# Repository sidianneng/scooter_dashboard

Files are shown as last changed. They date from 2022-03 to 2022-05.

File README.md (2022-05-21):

# 滑板车定制仪表盘

## 1 项目概述

该仪表盘基于ninebot的E22滑板车进行设计。

**在兼容原始仪表盘的所有功能的前提下，同时将官方手机端的功能也集成到了其中。**

这样极大的提高了使用的便捷性。

## 2 功能介绍
该仪表盘共计有4个界面，分别对应不同的功能：
### 2.1 主界面
主界面中100%还原了官方仪表盘的原始状态。支持显示的内容如下：
* 实时速度
* 电量情况
* 充电情况
* 速度单位
* 蓝牙状态
* 运动模式
* 错误提示

图片如下：

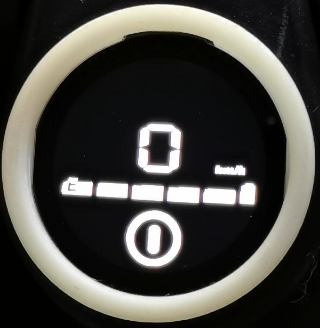
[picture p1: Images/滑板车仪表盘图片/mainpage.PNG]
mainpage


### 2.2 上锁解锁界面
该界面可以通过长按触摸屏实现对滑板车的上锁解锁，避免了以往手机app连接的繁琐操作。

图片如下：

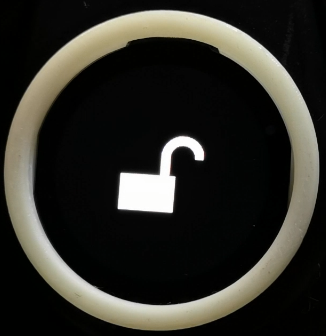
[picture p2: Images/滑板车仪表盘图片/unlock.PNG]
unlock

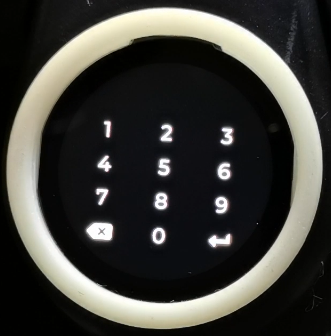
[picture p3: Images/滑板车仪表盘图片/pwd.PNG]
pwd


### 2.3 续航数据显示界面
该界面显示了如下信息：
* 剩余续航
* 剩余电量
* 总里程数

图片如下：

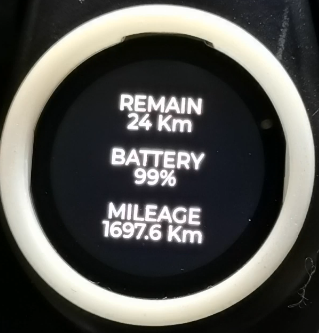
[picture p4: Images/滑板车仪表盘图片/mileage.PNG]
mileage


### 2.4 设置界面
该界面实现了滑板车的一些配置功能，具体如下：

* 开启关闭定速巡航
* 设置能量回收强度
* 设置上锁解锁密码

相关图片如下：

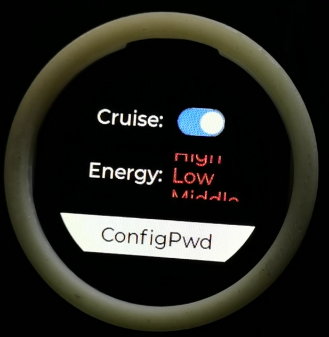
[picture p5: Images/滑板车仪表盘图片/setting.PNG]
setting

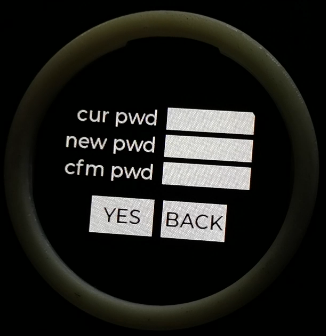
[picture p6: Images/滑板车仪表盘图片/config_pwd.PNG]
config_pwd


## 3 关键性功能原理介绍
该仪表盘中有两个核心功能点：

* 原始仪表盘数据解析
* 原始通讯协议数据解析

### 3.1 原始仪表盘数据解析
原始仪表盘的数据是通过蓝牙芯片控制一个数码管驱动芯片(TM1650)实现的，其中使用I2C作为通讯接口。我们通过解析其I2C通讯的数据内容，结合数码管芯片的数据手册。这样就能获取到完整的仪表盘数据了。

示意图如下：

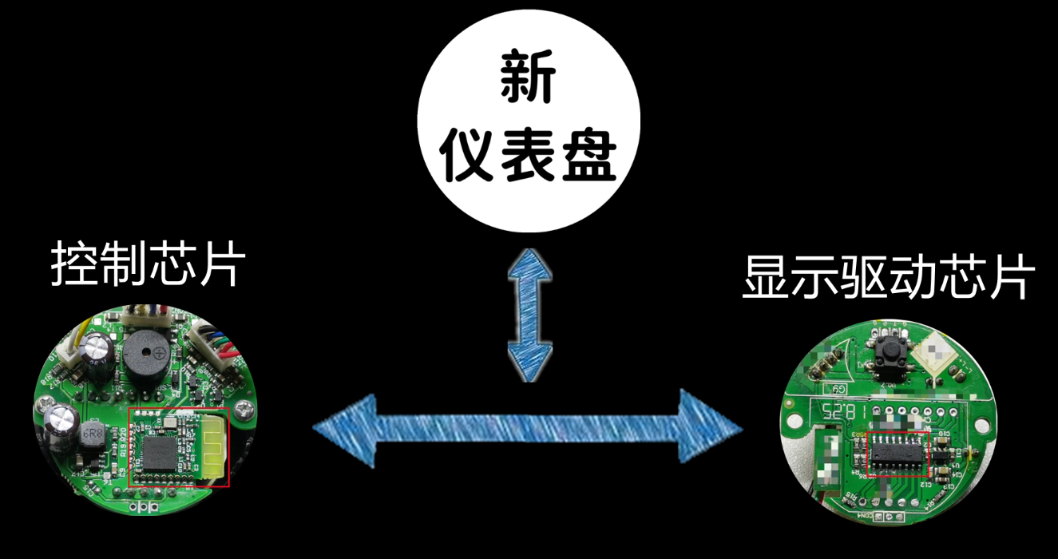
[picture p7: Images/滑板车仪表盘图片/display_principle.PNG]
display_principle


### 3.2 原始通讯协议数据解析
原始仪表盘和主板之间通过单线串口实现数据通讯，我们通过将新仪表盘连接到它们之间，通过截取和转发它们间的通讯内容，在必要时加入我们需要的数据，这样就能实现对滑板车的更多功能控制。

示意图如下：

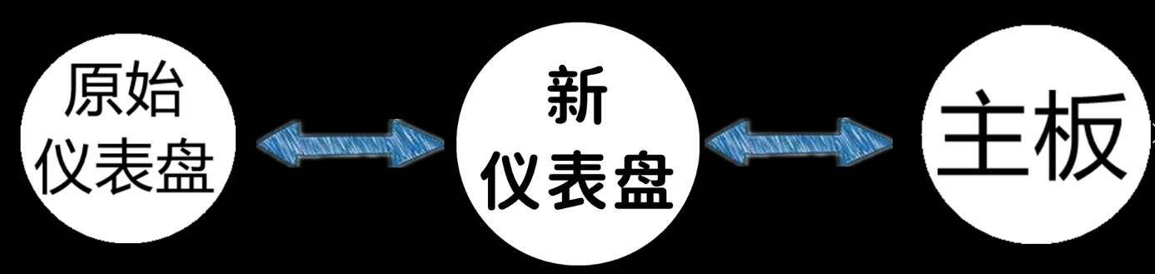
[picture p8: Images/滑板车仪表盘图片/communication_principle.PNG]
communication_principle


## 4 鸣谢
该项目的软件框架是基于[X-TRACK](https://github.com/FASTSHIFT/X-TRACK)进行二次开发的。

X-TRACK是一个很不错的开源项目，其代码逻辑实现非常清晰和优美，另外其处理issue的速度也非常快。在我开发的过程中提供了很多帮助。在这里对其表示衷心的感谢。希望该项目能越来越好。

***如果使用过程中有任何问题，欢迎在issue中进行提问~***

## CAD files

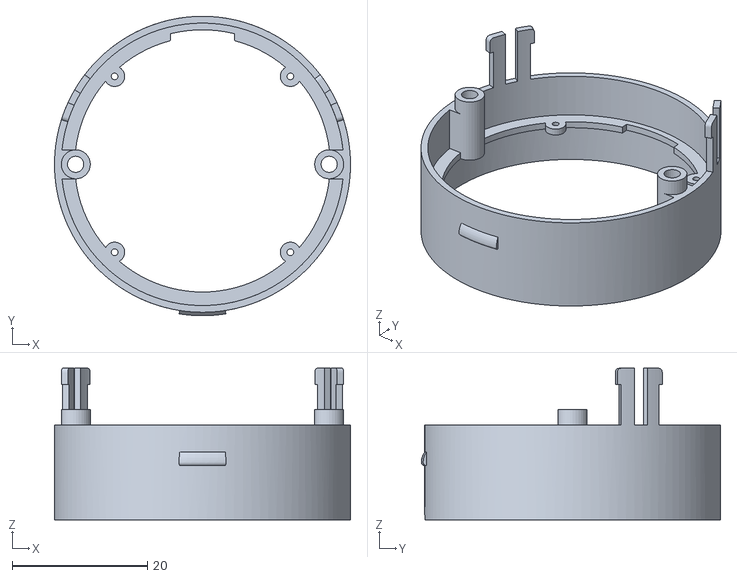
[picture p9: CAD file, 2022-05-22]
3D Model/scooter_panel_main v68.stl
43.7 x 44.2 x 22.4

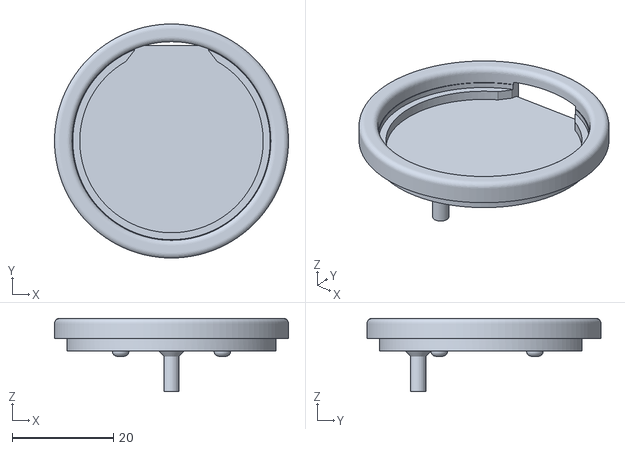
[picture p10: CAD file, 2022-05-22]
3D Model/scooter_panel_lcd v31.stl
46.2 x 46.2 x 14.5

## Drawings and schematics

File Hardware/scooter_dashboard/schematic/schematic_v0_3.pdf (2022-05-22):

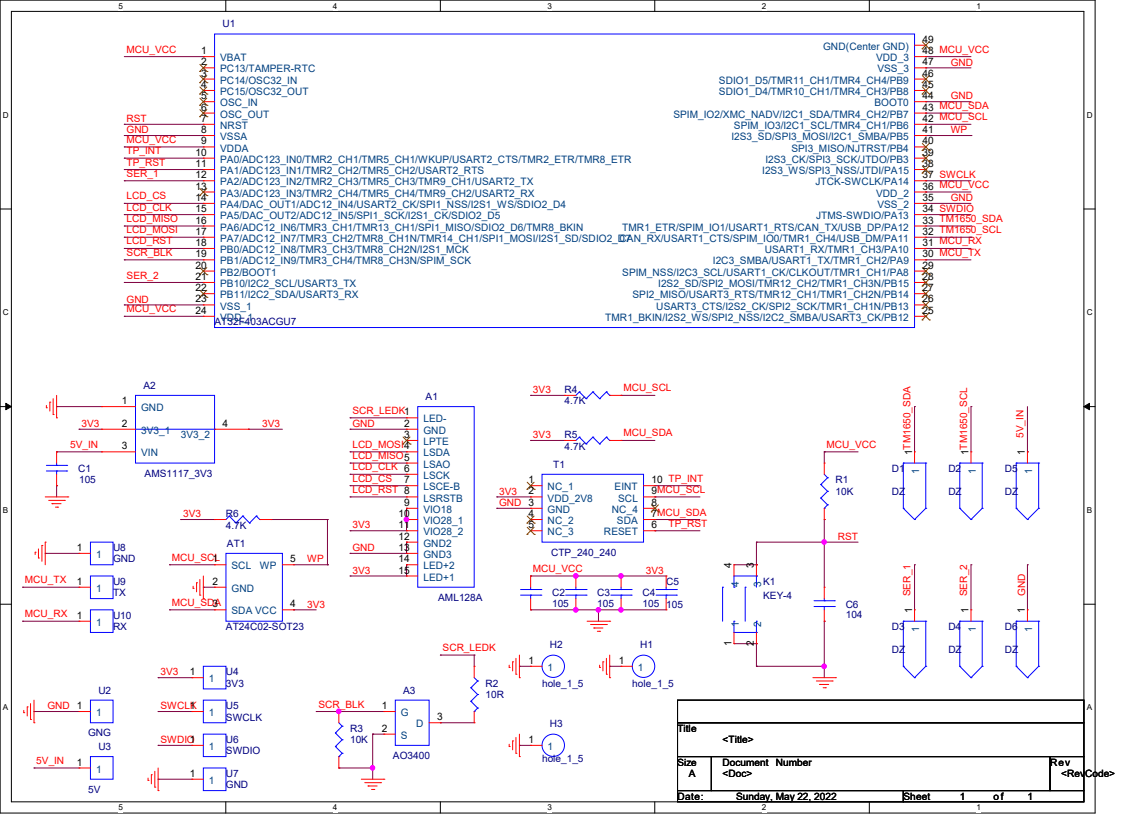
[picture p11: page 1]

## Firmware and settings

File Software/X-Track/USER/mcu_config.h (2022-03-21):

/*
 * MIT License
 * Copyright (c) 2019-2021 _VIFEXTech
 *
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
 * THE SOFTWARE IS PROVIDED "AS IS", WITHOUT WARRANTY OF ANY KIND, EXPRESS OR
 * IMPLIED, INCLUDING BUT NOT LIMITED TO THE WARRANTIES OF MERCHANTABILITY,
 * FITNESS FOR A PARTICULAR PURPOSE AND NONINFRINGEMENT. IN NO EVENT SHALL THE
 * AUTHORS OR COPYRIGHT HOLDERS BE LIABLE FOR ANY CLAIM, DAMAGES OR OTHER
 * LIABILITY, WHETHER IN AN ACTION OF CONTRACT, TORT OR OTHERWISE, ARISING FROM,
 * OUT OF OR IN CONNECTION WITH THE SOFTWARE OR THE USE OR OTHER DEALINGS IN THE
 * SOFTWARE.
 */
#if 1

#ifndef __MCU_CONFIG_H
#define __MCU_CONFIG_H

/*=========================
   MCU configuration
 *=========================*/

/* System tick */
#define SYSTICK_TICK_FREQ                   1000 // Hz
#define SYSTICK_PRIORITY                    0

/* Hardware Serial */
#define SERIAL_RX_BUFFER_SIZE               512
#define SERIAL_PREEMPTIONPRIORITY_DEFAULT   1
#define SERIAL_SUBPRIORITY_DEFAULT          3
#define SERIAL_CONFIG_DEFAULT               SERIAL_8N1

#define SERIAL_1_ENABLE                     1
#if SERIAL_1_ENABLE
#  define SERIAL_1_USART                    USART1
#  define SERIAL_1_IRQ_HANDLER_DEF()        void USART1_IRQHandler(void)
#endif

#define SERIAL_2_ENABLE                     0
#if SERIAL_2_ENABLE
#  define SERIAL_2_USART                    USART2
#  define SERIAL_2_IRQ_HANDLER_DEF()        void USART2_IRQHandler(void)
#endif

#define SERIAL_3_ENABLE                     0
#if SERIAL_3_ENABLE
#  define SERIAL_3_USART                    USART3
#  define SERIAL_3_IRQ_HANDLER_DEF()        void USART3_IRQHandler(void)
#endif

/* Wire (Software I2C) */
#define WIRE_USE_FULL_SPEED_I2C             0
#define WIRE_SDA_PIN                        PB7
#define WIRE_SCL_PIN                        PB6
#define WIRE_DELAY                          5
#define WIRE_BEGIN_TIMEOUT                  100 // ms
#define WIRE_BUFF_SIZE                      32

/* SPI Class */
#define SPI_CLASS_AVR_COMPATIBILITY_MODE    1
#define SPI_CLASS_PIN_DEFINE_ENABLE         0

#define SPI_CLASS_1_ENABLE                  1
#if SPI_CLASS_1_ENABLE
#  define SPI_CLASS_1_SPI                   SPI1
#endif

#define SPI_CLASS_2_ENABLE                  1
#if SPI_CLASS_2_ENABLE
#  define SPI_CLASS_2_SPI                   SPI2
#endif

#define SPI_CLASS_3_ENABLE                  0
#if SPI_CLASS_3_ENABLE
#  define SPI_CLASS_3_SPI                   SPI3
#endif

/* WString */
#define WSTRING_MEM_CUSTOM                  1
#if WSTRING_MEM_CUSTOM
#  define WSTRING_MEM_INCLUDE               "lvgl/lvgl.h"
#  define WSTRING_MEM_REALLOC               lv_mem_realloc
#  define WSTRING_MEM_FREE                  lv_mem_free
#endif

/* Print */
#define PRINT_PRINTF_BUFFER_LENGTH          128

/* GPIO */
#define GPIO_MAX_SPEED_DEFAULT              GPIO_MaxSpeed_50MHz

/* External Interrupt  */
#define EXTI_PREEMPTIONPRIORITY_DEFAULT     2
#define EXTI_SUBPRIORITY_DEFAULT            1

/* Timer Interrupt */
#define TIMER_PREEMPTIONPRIORITY_DEFAULT    0
#define TIMER_SUBPRIORITY_DEFAULT           3

/* Tone */
#define TONE_TIMER_DEFAULT                  TIM1
#define TONE_PREEMPTIONPRIORITY_DEFAULT     0
#define TONE_SUBPRIORITY_DEFAULT            1

/* PWM */
#define PWM_DUTYCYCLE_DEFAULT               1000
#define PWM_FREQUENCY_DEFAULT               10000

/* Digital Tube(TM1650) decode */
#define DIGITAL_TUBE_SCL_PIN								PA11
#define DIGITAL_TUBE_SDA_PIN								PA12

#endif

#endif

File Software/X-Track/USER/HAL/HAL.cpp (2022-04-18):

#include "HAL.h"
#include "App/Version.h"
#include "MillisTaskManager/MillisTaskManager.h"

static MillisTaskManager taskManager;

#if CONFIG_SENSOR_ENABLE
static bool IsWireInitSuccess = false;

static void HAL_Sensor_Init()
{
    IsWireInitSuccess = (HAL::I2C_Scan() > 0);

    if(!IsWireInitSuccess)
    {
        Serial.println("I2C: disable sensors");
        return;
    }

#if CONFIG_SENSOR_IMU_ENABLE
    HAL::IMU_Init();
#endif

#if CONFIG_SENSOR_MAG_ENABLE
    HAL::MAG_Init();
#endif
}

static void HAL_SensorUpdate()
{
    if(!IsWireInitSuccess)
    {
        return;
    }

#if CONFIG_SENSOR_IMU_ENABLE
    HAL::IMU_Update();
#endif

#if CONFIG_SENSOR_MAG_ENABLE
    HAL::MAG_Update();
#endif
}
#endif

static void HAL_TimerInterrputUpdate()
{
    HAL::Power_Update();
    HAL::Encoder_Update();
    HAL::Audio_Update();
}

void HAL::HAL_Init()
{
    Serial.begin(115200);
    Serial.println(VERSION_FIRMWARE_NAME);
    Serial.println("Version: " VERSION_SOFTWARE);
    Serial.println("Author: "  VERSION_AUTHOR_NAME);
    Serial.println("Project: " VERSION_PROJECT_LINK);

    FaultHandle_Init();

    Memory_DumpInfo();
	
		/*
			We need to init the hardware of scooter.
			Because we need to make sure the hardware ready
			to work before the origin hardware of scooter 
			start working.
		*/
		HalfDuplexSerial_Init();
		Scooter_Specify_Hardware_Init();

	  EEPROM_Init();
    //Power_Init();
    Backlight_Init();
    //Encoder_Init();
    //Clock_Init();
    //Buzz_init();
    //GPS_Init();
#if CONFIG_SENSOR_ENABLE
    HAL_Sensor_Init();
#endif
    //Audio_Init();
    //SD_Init();

		TouchPanel_Init();
    Display_Init();
		
		taskManager.Register(Scooter_Update, 500);
#if CONFIG_SENSOR_ENABLE
    taskManager.Register(HAL_SensorUpdate, 1000);
#endif
    taskManager.Register(Memory_DumpInfo, 1000);

    Timer_SetInterrupt(CONFIG_HAL_UPDATE_TIM, 10 * 1000, HAL_TimerInterrputUpdate);
    Timer_SetEnable(CONFIG_HAL_UPDATE_TIM, true);
}

void HAL::HAL_Update()
{
    taskManager.Running(millis());
}

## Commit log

2021-12-15 close the animation and add the test button for hardware debug
2021-12-16 fix the keil compile error of demo button for scooterpanel
    [HAL.cpp, lv_port_indev.cpp]
2021-12-21 change the i2c gpio to PB8/PB9
2022-03-18 add the battery capacity display of scooter
2022-03-19 scooter battery capacity function works fine now
2022-04-04 fix the simulator project
    [HAL_HalfDuplexSerial.cpp]
2022-04-04 fix the UI switch problem Problem description: After I swipe left to switch the UI from ScooterLock to ScooterSysinfo. If I want to back to ScooterLock.I need to swipe right for two times.
2022-04-09 Fix the log error when a pop operation is detected Reproduce steps: 1 open the micro of DC_LOG_INFO in DataCenterLog.h 2 run the simulator project 3 click the SystemInfos button to enter the Systemin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
    What we need is "PagePOP is detect, move Page(Diaplate) to foreground"
2022-04-15 add the new icon of power key
2022-04-15 change the timer cycle for better performance
2022-04-16 fix the project config of image power_key&switch for keil
2022-04-17 add the driver of 24c01 and fix the compile error
2022-04-18 add the pwd change button in systemsetting
2022-04-21 current pwd can pass from pwdcfg to pwdinput now
2022-05-22 upload the 3D model,schematic, pcb files
    [scooter_panel_lcd v31.stl, scooter_panel_main v68.stl, 外壳-主体.STL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]
